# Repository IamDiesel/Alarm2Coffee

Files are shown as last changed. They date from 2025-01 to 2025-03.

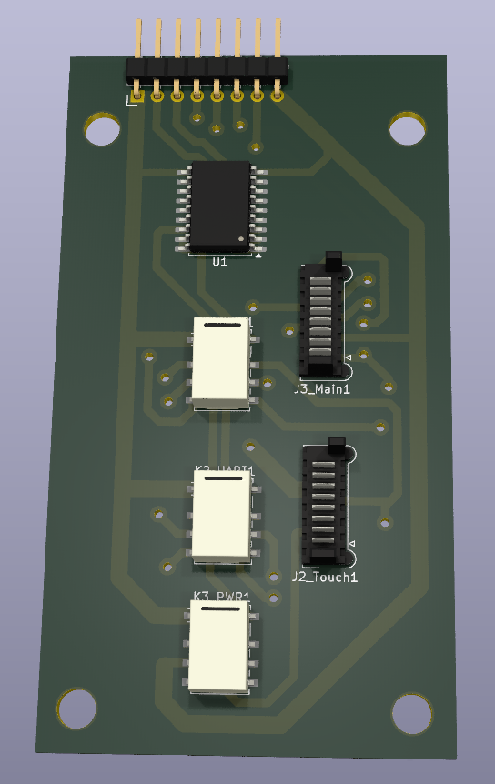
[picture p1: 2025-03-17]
PCB_SCH/PCB_Render.png

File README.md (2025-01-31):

# Power on your Philips 2200 Coffeemachine when your smartphone-alarm goes off - via Raspberry Pi and Home-Assistant #
The following readme describes how to setup a raspberry pi / philips 2200 coffeemachine home assistant automation from scratch (incl. setting up home assistant on a Raspberry Pi5). Btw. thanks to https://github.com/TillFleisch/ESPHome-Philips-Smart-Coffee who gave me some inspiration / information on the coffee machine's UART-protocol.
This project is also capable of displaying the current coffeemachine state and remotly operating the coffeemachine via a smartphone's home assistant app:


### Requirements: ###
- Coffee-Machine: Philips 2200
- MITM (inject & passthrough): Inject coffee selection commands and read current coffee configuration
- Use home assistant for automation and hub to the smartphone alarm
- Additional Fail-Safe mechanism in case RPi is dead and  the MITM configuration must be bridged

### Components used: ###
- Raspberry Pi5 + SD Card
- PicoFlex 90325-0008 socket
- Molex 92315-0815, Picoflex, ribbon cable 150mm
- AZDelivery 3 x 4-Relais Modul 5V
- LUCKFOX DSI Capacitive 7 inch Touch Screen with Case
- Jumper Wire / cables / glue / screws / ...
- If Home Assistant should be connected via wifi: Brostrend AX1800 (External USB Wifi Antenna)

## Install home assistant on Raspberry Pi 5 ##
- Use Pi Imager to flash SD card (see https://developbyter.com/home-assistant-auf-raspberry-pi-installieren-und-einrichten/) 
- create empty file called "ssh" on sd card "bootfs"
- tell router to give RPi a constant IP address
- connect via ssh to RPi (ssh user@ipadress)
- update: sudo apt-get update && sudo apt-get upgrade -y
- install dependencies:
  - sudo apt-get install jq wget curl avahi-daemon udisks2 libglib2.0-bin network-manager dbus apparmor -y
  - sudo apt-get install systemd-journal-remote
- reboot: sudo reboot
- deactivate mac address randomisation:
  - sudo nano /etc/NetworkManager/conf.d/100-disable-wifi-mac-randomization.conf
  - Content:

~~~
[connection]
wifi.mac-address-randomization=1
[device]
wifi.scan-rand-mac-address=no
)
~~~

- install docker & add user:
  
~~~
curl -fsSL https://get.docker.com -o get-docker.sh
sudo sh get-docker.sh
docker –version
sudo usermod -aG docker <user>
~~~

- Download OS-Agent on raspberry pi: wget https://github.com/home-assistant/os-agent/releases/download/1.6.0/os-agent_1.6.0_linux_aarch64.deb
- install: sudo dpkg -i os-agent_1.6.0_linux_aarch64.deb

- install additional dependencies:

~~~
sudo apt install \
apparmor \
bluez \
cifs-utils \
curl \
dbus \
jq \
libglib2.0-bin \
lsb-release \
network-manager \
nfs-common \
systemd-journal-remote \
systemd-resolved \
udisks2 \
wget -y
~~~

- install home assistant superviced (https://github.com/home-assistant/supervised-installer/releases/download/2.0.0/homeassistant-supervised.deb)
  - sudo dpkg -i homeassistant-supervised.deb
  - during installation: choose raspberrypi5-64
  - reboot
- open home assistant in your browser: <ipadress_of_pi>:8123
- download and install smartphone app via QR-Code
- Show home assistant on startup on the 7" display:
  - configure autostart: sudo nano /etc/xdg/lxsession/LXDE-pi/autostart
    - add the following lines:
      
~~~
@unclutter
@xset s off
@xset -dpms
@xset s noblank
@chromium-browser --noerrdialogs --check-for-update-interval=31536000 --disable-infobars --kiosk http://127.0.0.1:8123/
~~~
  if you want to keep a 5min display off timer, use the following settings:
~~~
@unclutter
@xset s off
@xset -dpms
@xset s 300 300
@xset s blank
@chromium-browser --noerrdialogs --check-for-update-interval=31536000 --disable-infobars --kiosk http://127.0.0.1:8123/
~~~

  - activate autologin on pi

~~~
cd /usr/share/hassio/homeassistant/
sudo nano configuration.yaml
~~~

  - add the following lines
    
~~~

homeassistant:
  auth_providers:
    - type: homeassistant
    - type: trusted_networks
      trusted_networks:
        - 192.168.2.0/24  # Example network, adjust to your network range
        - fd00::/8
      trusted_users:
        127.0.0.1: 6a24b8e59e2c45328cd1s97ds0b71221  # Map the IP address to the user ID
        192.168.2.43: 6a24b8249e22445x1cd1797123471221  # Map the IP address to the user ID
      allow_bypass_login: true
  ~~~
  
- install 7inch display (https://wiki.luckfox.com/):
  - sudo nano /boot/config.txt
  - add the following lines:
 
~~~
dtoverlay=vc4-kms-v3d
dtoverlay=vc4-kms-dsi-7inch
~~~
## Install Wifi Antenna ##
Installation guide see https://linux.brostrend.com/
For me, the command from the installation guide threw an error.
Command:
~~~
 sh -c 'wget linux.brostrend.com/install -O /tmp/install && sh /tmp/install'
~~~
Error:
~~~
Setting up initramfs-tools (0.142+rpt3+deb12u1) ...
update-initramfs: deferring update (trigger activated)
Processing triggers for initramfs-tools (0.142+rpt3+deb12u1) ...
update-initramfs: Generating /boot/initrd.img-6.6.62+rpt-rpi-v8
mkinitramfs: failed to determine device for /
mkinitramfs: workaround is MODULES=most, check:
grep -r MODULES /etc/initramfs-tools

Error please report bug on initramfs-tools
Include the output of 'mount' and 'cat /proc/mounts'
update-initramfs: failed for /boot/initrd.img-6.6.62+rpt-rpi-v8 with 1.
dpkg: error processing package initramfs-tools (--configure):
 installed initramfs-tools package post-installation script subprocess returned error exit status 1
Errors were encountered while processing:
 initramfs-tools
E: Sub-process /usr/bin/dpkg returned an error code (1)
Aborting, command failed: apt install --reinstall --yes --no-install-recommends ./rtl8852bu-dkms.deb

===================================================
 ERROR: The driver was NOT successfully installed!
===================================================
1) Please select ALL the text in this terminal, then right click with the
   mouse and select Copy, and finally paste all the text in an email to:
   support@brostrend.com
2) Please also attach this autogenerated log file to the email:
   /tmp/troubleshooting.txt
   If you want to view it, run:
   xdg-open /tmp/troubleshooting.txt
3) Some common issues are documented in:
   https://linux.brostrend.com/troubleshooting/
~~~
Solution:
~~~
sudo nano /etc/initramfs-tools/initramfs.conf
~~~
And set „MODULES=dep“ to „MODULES=most“.
Next, the wifi interface needs to be configured:
- deactivate wlan0: sudo ip link set wlan0 down
- Router: remove static ip for old interface and set static ip for the new interface (e.g. 192.168.2.43)
- In Home Assistant: Go to settings->system->network.
  - Reset configuration for wlan0
  - Set static ip for wlan1
- Configure wifi connection:
  - remove all wlan0 profiles (in GUI top right corner, click on the wifi symbol and delete all wlan0 profiles) 
  - sudo nmtui
  - edit connection
  - select wifi->preconficured --> hit "edit"
  - Find the wlan1 device name (for me it is wlxc83a35b569cd (C8:3A:35:B5:69:CD)
  - Enter SSID
  - Enter WIFI-password
  - set manual ip adress: 192.168.2.43/24
  - set Gateway: your routers ip
  - set DNS servers: your routers ip
 
- If chromium doest start on boot: rm -rf ~/.config/chromium/Singleton*

## configure home assistant ##
### Create entities (German) ###
Create entities (Einstellungen -> Geräte und Dienste -> Helfer)



### Create Automations (German) ###



### setup alarm (Android) ###
- Open the Home Assistant App menu and select Settings
- Go to Companion App
- Select Manage Sensors
- Find the Next Alarm sensor
- Enable the Next Alarm sensor
- Create automation: „Einstellungen“->“Automatisierung & Szenen“->“Automatisierung erstellen““Neue Automatisierung“
  - Auslöser hinzufügen: “Andere Auslöser“-->“Template“
  - Template code:
  
   ~~~
    {{(now()+timedelta(0,60)).strftime('%a %h %d %H:%M %Z %Y') == (((state_attr('sensor.pixel_9_pro_next_alarm', 'Time in Milliseconds') | int / 1000) ) | timestamp_custom('%a %h %d %H:%M %Z %Y'))}}
   ~~~
   
  - add action:


### setup alarm (iOs) ###
The focus sensor can be used to determine when the alarm went off.
- Create iOS shortcut named "HAss focus": deactivate focus
- Create iOS automation that executes the "Hass focus" everytime an alarm goes off
Now the companion app focus sensor of the iOS device can be used to trigger automations in Home-Assistant
- Create Home-Assistant automation:







# Disassemble coffee machine #
The coffee machine's display can be disassembled using a plastic tool.



The wiring between display and mainboard is as follows:



Communication is run via UART @115200
The state of the coffeemachine ist sent from the mainboard to the display. The button events are sent from the display to the mainboard.

# Communication #
## Mainboard -> Display



## Display -> Mainboard



### On / Off ###

~~~
On / Off Beep: d5 55 0a 00 00 03 02 00 00 00 32 25
Power on without cleaning cycle: d5 55 01 00 00 03 02 00 00 00 19 10	
Power Off no Cleaning cycle?: d5550000000302010000210c
~~~

### Drink Selection: ###

~~~
Select Nothing: 		d5 55 00 00 00 03 02 00 00 00 2d 01
Select Espresso:	d5 55 00 00 00 03 02 02 00 00 35 1a 	Nachricht wird 13x gesendet
perl -e 'print pack "H*", "d5550000000302020000351a"' > /dev/ttyUSB2

Hot Water:		d5 55 00 00 00 03 02 04 00 00 1d 36
Select Coffee:		d5 55 00 00 00 03 02 08 00 00 05 2b	Nachricht wird 8x gesendet
Steam:			d5 55 00 00 00 03 02 10 00 00 35 11	Nachricht wird 32x gesendet
~~~

### Settings: ###

~~~

d5 55 00 00 00 03 02 00 02 00 35 18	Bean Size
d5 55 00 00 00 03 02 00 04 00 1c 32	Coffee Size
Play:
d5 55 00 00 00 03 02 00 00 01 25 05 	Play-Button (espresso, 39x)
perl -e 'print pack "H*", "d55500000003020000012505"' > /dev/ttyUSB2
~~~

For both mainboard messages and display messages the CRC algorithm is currently unknown. So it might be necessary to record the messages individually.

## Connect relais, UART and power ##

The relayboard 1 is used as a failsafe when the pi does not power on. In that case the UART connection will be without the MITM and therby the mainboard is directly connected to the display. When the relay is activated the raspberry pi acts as MITM between mainboard and display.
Relayboard 2 is used to reset the display when activated via power on command incection. A power cycle will activate the display. This relay is also failsafe for the case, that RPi is powered off, since Display GND is connected to the Relay-Normally-Closed Pin and Relay-Common is connected to the Mainboard GND.
Here is the connection diagram:



## Activate UART2/3 and GPIO on RPi5 & ## 

Add the following lines via "sudo nano /boot/config.txt":



As a result the GPIO configuration will be as follows:
- ttyAMA2	Display	Pin 7 (GPIO 4)	TX
- ttyAMA2	Display	Pin 29 (GPIO 5)	RX
- ttyAMA3	Mainboard	Pin 24 (GPIO 8)	TX
- ttyAMA3	Mainboard	Pin 21 (GPIO 9)	RX

- In order to use GPIO on RPi5 another package is required: .coffee/bin/pip install rpi-lgpio
- It could be necessary to uninstall the RPi GPIO first: .coffee/bin/pip uninstall Rpi.GPIO

## Setup Home Assistant API / install the required python packages ##

- Create a longliving HAss token in HAss: Profil->Sicherheit
  - safe this token in a file called "HASS_Token.py" with: token = "asdjalksdjkasjdklasjd your token asdlkalösdkaölsd"
- Create venv:  python3 -m venv .coffee
- install Home assistant: .coffee/bin/pip install homeassistant_api
- install pyserial: .coffee/bin/pip install pyserial

## Home Assistant WIFI Stability Issues ##
Home Assistant started beeing offline from time to time. Where the device was not reachable via ssh or the home assistant app.
The only thing that seemed to help was a wifi reset. So I wrote a little script that (e.g.) pings the local router. In case the router is not reachable the script will reset wifi, making the HAss available again.

## Finish ##

WhatsApp Bild 2025-01-12 um 21 23 38_4eb5911e

- Thats it. Now run Philips_2200.py and the RPI will inject the respective display commands, when the respective Home Assistant buttons are pushed. If no button is pushed, the RPi will forward all messages from display to mainboard and vice versa. In Addition a alarm will trigger a power on command sent to the coffee machine.
- the relay boards fit nicely behind the display. I glued screws on the backside of the display module in order to fit the relay boards to the display.
- In order to run the python script on startup the following lines can be added to rc.local via sudo nano /etc/rc.local:
~~~
sudo bash -c '/home/youruser/.coffee/bin/python3 /home/youruser/Documents/philips_pi/Philips_2200.py > /home/fuchsi/Documents/philips_pi/alarm2coffee.log 2>&1' &
~~~
Of course the path must be set to your local Philips_2200.py. In addition Wifi_Reset.py must be in the same folder as Philips_2200.py.
- Also a dashboard can be created in order to interact with the coffeemachine via smartphone. Here is mine:

~~~

views:
  - type: sections
    max_columns: 2
    title: Kaffee
    path: kaffee
    icon: mdi:coffee
    sections:
      - type: grid
        cards:
          - type: tile
            entity: input_button.philips_display_power_btn
            name: Power On
            icon_tap_action:
              action: toggle
            tap_action:
              action: toggle
            hide_state: true
          - type: tile
            entity: input_button.philips_display_power_off_btn
            name: Power Off
            tap_action:
              action: toggle
            hide_state: true
          - show_name: true
            show_icon: true
            type: button
            tap_action:
              action: perform-action
              perform_action: automation.trigger
              target:
                entity_id: automation.philips_display_steam_event_helper
              data:
                skip_condition: true
            entity: input_boolean.philips_mainboard_espresso_led
            show_state: false
            name: Espresso
            icon: mdi:cup
          - show_name: true
            show_icon: true
            type: button
            tap_action:
              action: perform-action
              perform_action: automation.trigger
              target:
                entity_id: automation.philips_event_coffee_btn
              data:
                skip_condition: true
            entity: input_boolean.philips_mainboard_coffee_led
            show_state: false
            name: Coffee
            icon: mdi:coffee
          - show_name: true
            show_icon: true
            type: button
            tap_action:
              action: perform-action
              perform_action: automation.trigger
              target:
                entity_id: automation.philips_event_hot_water_btn
              data:
                skip_condition: true
            entity: input_boolean.philips_mainboard_hot_water_led
            show_state: false
            name: Hot Water
            icon: mdi:tea-outline
          - show_name: true
            show_icon: true
            type: button
            tap_action:
              action: perform-action
              perform_action: automation.trigger
              target:
                entity_id: automation.neue_automatisierung
              data:
                skip_condition: true
            entity: input_boolean.philips_mainboard_steam_led
            show_state: false
            name: Steam
            icon: mdi:weather-windy
      - type: grid
        cards:
          - show_name: true
            show_icon: true
            type: button
            tap_action:
              action: toggle
            entity: input_button.input_button_philips_display_play_btn
            grid_options:
              columns: 12
              rows: 2
            name: Start
          - type: conditional
            conditions:
              - condition: state
                entity: input_select.philips_bean_led
                state: '1'
            grid_options:
              columns: 6
              rows: 1
            card:
              show_name: true
              show_icon: true
              type: button
              tap_action:
                action: toggle
              entity: input_button.philips_display_bean_btn
              icon: mdi:network-strength-1
              hold_action:
                action: toggle
              name: Strength
          - type: conditional
            conditions:
              - condition: state
                entity: input_select.philips_bean_led
                state: '2'
            grid_options:
              columns: 6
              rows: 1
            card:
              show_name: true
              show_icon: true
              type: button
              tap_action:
                action: toggle
              entity: input_button.philips_display_bean_btn
              icon: mdi:network-strength-3
              hold_action:
                action: toggle
              name: Strength
          - type: conditional
            conditions:
              - condition: state
                entity: input_select.philips_bean_led
                state: '3'
            grid_options:
              columns: 6
              rows: 1
            card:
              show_name: true
              show_icon: true
              type: button
              tap_action:
                action: toggle
              entity: input_button.philips_display_bean_btn
              icon: mdi:network-strength-4
              hold_action:
                action: toggle
              name: Strength
          - type: conditional
            conditions:
              - condition: state
                entity: input_select.philips_bean_led
                state: 'Off'
            grid_options:
              columns: 6
              rows: 1
            card:
              show_name: true
              show_icon: true
              type: button
              tap_action:
                action: none
              entity: input_button.philips_display_bean_btn
              icon: mdi:cancel
              hold_action:
                action: none
              name: Strength
          - type: conditional
            conditions:
              - condition: state
                entity: input_select.philips_cup_size_led
                state: '1'
            grid_options:
              columns: 6
              rows: 1
            card:
              show_name: true
              show_icon: true
              type: button
              tap_action:
                action: toggle
              entity: input_button.philips_display_cup_btn
              icon: mdi:network-strength-1
              hold_action:
                action: toggle
              name: Size
          - type: conditional
            conditions:
              - condition: state
                entity: input_select.philips_cup_size_led
                state: '2'
            grid_options:
              columns: 6
              rows: 1
            card:
              show_name: true
              show_icon: true
              type: button
              tap_action:
                action: toggle
              entity: input_button.philips_display_cup_btn
              icon: mdi:network-strength-3
              hold_action:
                action: toggle
              name: Size
          - type: conditional
            conditions:
              - condition: state
                entity: input_select.philips_cup_size_led
                state: '3'
            grid_options:
              columns: 6
              rows: 1
            card:
              show_name: true
              show_icon: true
              type: button
              tap_action:
                action: toggle
              entity: input_button.philips_display_cup_btn
              icon: mdi:network-strength-4
              hold_action:
                action: toggle
              name: Size
          - type: conditional
            conditions:
              - condition: state
                entity: input_select.philips_cup_size_led
                state: 'Off'
            grid_options:
              columns: 6
              rows: 1
            card:
              show_name: true
              show_icon: true
              type: button
              tap_action:
                action: none
              entity: input_button.philips_display_cup_btn
              icon: mdi:cancel
              hold_action:
                action: none
              name: Size
          - type: conditional
            conditions:
              - condition: state
                entity: input_boolean.philips_double_coffee_led
                state: 'on'
            grid_options:
              columns: 6
              rows: 1
            card:
              show_name: true
              show_icon: true
              type: button
              tap_action:
                action: none
              entity: input_boolean.philips_double_coffee_led
              name: Coffee
              hold_action:
                action: none
              icon: mdi:dice-2
          - type: conditional
            conditions:
              - condition: state
                entity: input_boolean.philips_double_espresso_led
                state: 'on'
            grid_options:
              columns: 6
              rows: 1
            card:
              show_name: true
              show_icon: true
              type: button
              tap_action:
                action: none
              entity: input_boolean.philips_double_coffee_led
              name: Espresso
              hold_action:
                action: none
              icon: mdi:dice-2
          - type: conditional
            conditions:
              - condition: state
                entity: input_select.philipps_water_empty_led
                state: Water empty
            grid_options:
              columns: 6
              rows: 1
            card:
              show_name: true
              show_icon: true
              type: button
              tap_action:
                action: none
              entity: input_select.philipps_water_empty_led
              name: No Water
              hold_action:
                action: none
              icon: mdi:water-off
          - type: conditional
            conditions:
              - condition: state
                entity: input_select.philipps_error_led
                state: Waste full
            grid_options:
              columns: 6
              rows: 1
            card:
              show_name: true
              show_icon: true
              type: button
              tap_action:
                action: none
              entity: input_boolean.philips_waste_helper_led
              name: Waste full
              hold_action:
                action: none
              icon: mdi:delete-variant
          - type: conditional
            conditions:
              - condition: state
                entity: input_select.philipps_error_led
                state: Error active
            grid_options:
              columns: 6
              rows: 1
            card:
              show_name: true
              show_icon: true
              type: button
              tap_action:
                action: none
              entity: input_boolean.philips_error_helper_led
              name: Error
              hold_action:
                action: none
              icon: mdi:alert-circle
        column_span: 1
      - type: grid
        cards:
          - type: heading
            heading_style: title
            icon: mdi:alarm
            badges:
              - type: entity
                entity: input_boolean.philips_alarm_daniel
              - type: entity
                entity: sensor.pixel_9_pro_next_alarm
              - type: entity
                show_state: true
                show_icon: true
                entity: input_boolean.philips_alarm_fox
            heading: Mit Wecker einschalten
          - type: tile
            entity: input_boolean.philips_alarm_daniel
            tap_action:
              action: toggle
            name: Alarm2Coffee Daniel
            grid_options:
              columns: 12
              rows: 1
          - type: tile
            entity: input_boolean.philips_alarm_fox
            tap_action:
              action: toggle
            name: Alarm2Coffee Fox
            grid_options:
              columns: 12
              rows: 1
          - type: tile
            entity: sensor.pixel_9_pro_next_alarm
            grid_options:
              columns: 12
              rows: 2
            name: Nächster Wecker Daniel
            hide_state: false
            show_entity_picture: false
            vertical: true
            state_content:
              - state
              - Local Time

~~~

# TODOs #
- [ ] Create relay-circuit-board to avoid messy wiring (also 3 relays are unused)
- [ ] Refactor python software
  - [x] check for HAss availability on startup
  - [ ] refactor SW components (file / component is too big)
  - [ ] further evaluate power cycle code
  - [x] Read coffee strength and display this information in home assistant
  - [x] Read cup size and display this information in home assistant
  - [x] Read 1x / 2x and drink selection information and display this information in home assistant
  - [x] Check Home Assistant loosing WIFI connection to home net
    - [x] Write script to reset wifi when loosing connection to gateway
    - [x] evaluate power settings

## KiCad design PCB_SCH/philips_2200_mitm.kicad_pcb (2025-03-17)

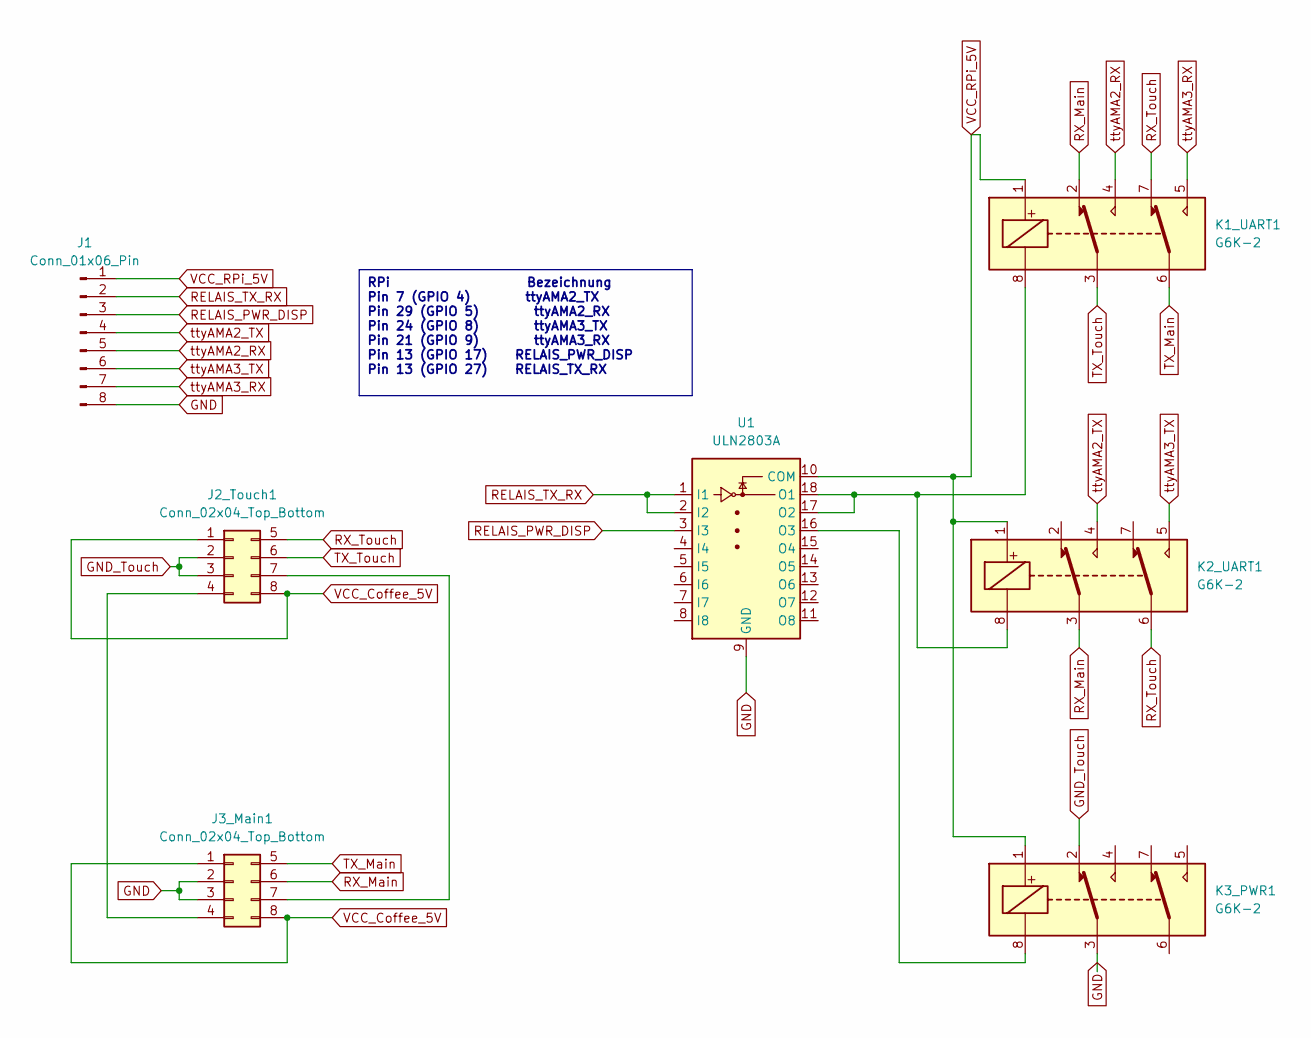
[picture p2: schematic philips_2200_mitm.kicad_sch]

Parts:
J1: Conn_01x06_Pin; PinHeader_1x08_P2.54mm_Horizontal
J2_Touch1, J3_Main1: Conn_02x04_Top_Bottom; Molex_Picoflex_90325-0008_2x04_P1.27mm_Vertical
K1_UART1, K2_UART1, K3_PWR1: G6K-2; Relay_DPDT_Omron_G6K-2F-Y
U1: ULN2803A; SOIC-18W_7.5x11.6mm_P1.27mm

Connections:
GND: J1.8, J3_Main1.2, J3_Main1.3, K3_PWR1.3, U1.9 (GND)
GND_Touch: J2_Touch1.2, J2_Touch1.3, K3_PWR1.2
unnamed: J2_Touch1.4, J3_Main1.4
unnamed: J2_Touch1.7, J3_Main1.7
unnamed: K1_UART1.8, K2_UART1.8, U1.17 (O2), U1.18 (O1)
unnamed: K3_PWR1.8, U1.16 (O3)
RELAIS_PWR_DISP: J1.3, U1.3 (I3)
RELAIS_TX_RX: J1.2, U1.1 (I1), U1.2 (I2)
RX_Main: J3_Main1.6, K1_UART1.2, K2_UART1.3
RX_Touch: J2_Touch1.5, K1_UART1.7, K2_UART1.6
TX_Main: J3_Main1.5, K1_UART1.6
TX_Touch: J2_Touch1.6, K1_UART1.3
VCC_Coffee_5V: J2_Touch1.1, J2_Touch1.8, J3_Main1.1, J3_Main1.8
VCC_RPi_5V: J1.1, K1_UART1.1, K2_UART1.1, K3_PWR1.1, U1.10 (COM)
ttyAMA2_RX: J1.5, K1_UART1.4
ttyAMA2_TX: J1.4, K2_UART1.4
ttyAMA3_RX: J1.7, K1_UART1.5
ttyAMA3_TX: J1.6, K2_UART1.5

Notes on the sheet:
RPi Bezeichnung Pin 7 (GPIO 4) ttyAMA2_TX Pin 29 (GPIO 5) ttyAMA2_RX Pin 24 (GPIO 8) ttyAMA3_TX Pin 21 (GPIO 9) ttyAMA3_RX Pin 13 (GPIO 17) RELAIS_PWR_DISP Pin 13 (GPIO 27) RELAIS_TX_RX

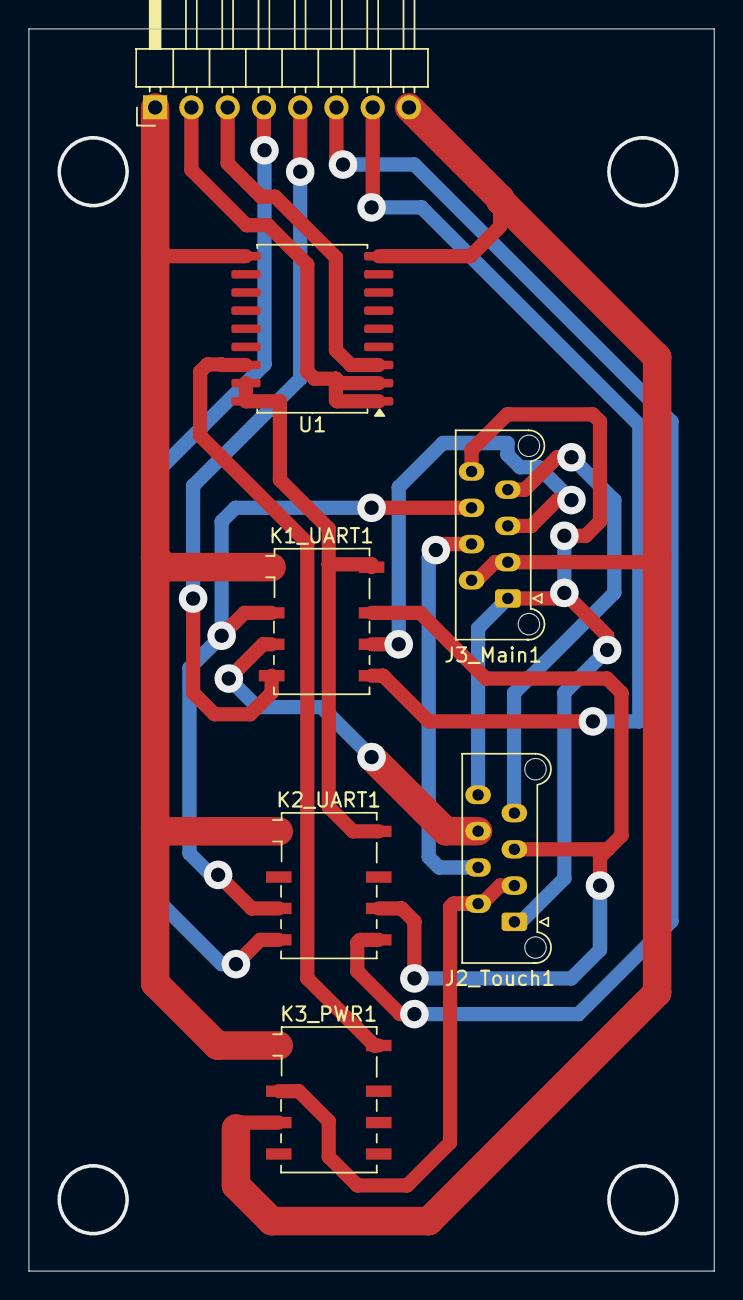
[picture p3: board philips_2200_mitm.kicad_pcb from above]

Board: 2 copper layers, 48.0 x 87.0 mm, 7 parts (0 on the bottom side), 18 nets.

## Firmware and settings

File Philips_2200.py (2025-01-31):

import os
from homeassistant_api import Client, State, errors
import serial
import subprocess
import sys
from HASS_Token import token
import RPi.GPIO as GPIO
import time
from threading import Thread
from Reset_Wifi import Wifi_Deamon

printSerial = False

class Philips_2200(Thread):
    def __init__(self,persistant_HASS_token, sn_serial_main=None, sn_serial_disp=None):

        GPIO.setmode(GPIO.BCM)  # GPIO Nummern statt Board Nummern
        self.RELAIS_PWR_DISP_GPIO = 17
        self.RELAIS_TX_RX_GPIO = 27 #RELAIS ON = MITM mode, #RELAIS Off = Normal mode

        self.sn_serial_main = sn_serial_main
        self.sn_serial_disp = sn_serial_disp
        
        self.persistant_HASS_token = persistant_HASS_token
        
        #send repetitions for the display commands
        self.cmd_rep = 20

        #mainboard protocol state definitions (mainboard -> display)
        self.preAmbelStates = {0xd5:'correct_0',0x55:'correct_1'}
        self.statesDrinkSelection = {0x00: 'Off', 0x03: 'Half Brightness', 0x07: 'Full Brightness', 0x38: 'Double', 0x3F:'Full Brightness'}
        self.beanLEDStates = {0x00:'1LED/Off', 0x38:'2LED', 0x3F:'3LED'}
        self.beanLEDStatesCtrl = {0x07: 'Show LED Group', 0x38: 'Powder Selected', 0x00:'Off'}
        self.sizeLEDStates = {0x00:'1LED/Off', 0x38:'2LED', 0x3F:'3LED', 0x07: 'TopLED'}
        self.sizeAquaLEDStates = {0x00: 'Off', 0x07:'Show LED Group',0x38:'Aqua Clean Orange'}
        self.calcCleanLEDStates = {0x00: 'Both Off', 0x38:'Calc / Clean orange', 0x07:'unknown'}
        self.emptyWaterLEDStates = {0x00: 'No error', 0x38:'Water empty'}
        self.wasteWarningLEDStates = {0x00: 'No error', 0x07:'Waste full', 0x38:'Error active'}
        self.playPauseLEDStates = {0x00:'Off', 0x07:'On'}
        
        #mainboard protocol (mainboard -> display)
        self.protocol = {0:self.preAmbelStates, 1:self.preAmbelStates,3:self.statesDrinkSelection, 4:self.statesDrinkSelection, 5:self.statesDrinkSelection, 6:self.statesDrinkSelection, 8:self.beanLEDStates, 9:self.beanLEDStatesCtrl, 10:self.sizeLEDStates, 11:self.sizeAquaLEDStates, 12:self.calcCleanLEDStates, 14:self.emptyWaterLEDStates, 15:self.wasteWarningLEDStates, 16:self.playPauseLEDStates}
        self.protocolNames = {0:'Pre_0',1:'Pre_1', 3:'Espresso LED', 4:'Hot Water LED', 5:'Coffe LED', 6:'Steam LED', 8:'Bean LED 0', 9:'Bean LED 1', 10:'Size LED', 11:'Size Aqua LED', 12:'Calc Clean', 14:'Water LED', 15:'Waste / Warning', 16:'Play LED'}
    
        #init serial
        if(sn_serial_main is None or sn_serial_disp is None):
            self.ser_display="/dev/ttyAMA2"
            self.ser_mainboard="/dev/ttyAMA3"
        else:           
            self.sn_serial_main = sn_serial_main
            self.sn_serial_disp = sn_serial_disp
            self.ser_mainboard = self.getSerialDeviceBySerialnumber(self.sn_mainboard)#"/dev/ttyUSB0" #TX_mainboard to RX_Pi_0, RX_mainboard to TX_Pi_0 
            self.ser_display = self.getSerialDeviceBySerialnumber(self.sn_display)
        self.__init_serial()
        self.__init_relais()
        self.__relais_on()
        
        self._running = False
        
        #helper for reading and setting HASS entities, blocks program until HAss is online
        self.hass_helper = self.HASS_Helper(self.persistant_HASS_token)
        #if a button was pressed inside HASS, this variable will be set to the corresponding display serial command
        self.next_cmd = None
        super(Philips_2200, self).__init__()

        #TODO enable relais for intercepting TX/RX

    def __init_serial(self):

        try:
            self.dev_display = serial.Serial(self.ser_display, write_timeout=1)   
            self.dev_mainboard = serial.Serial(self.ser_mainboard,write_timeout=1)
            self.dev_mainboard.baudrate = 115200
            self.dev_mainboard.bytesize = 8
            self.dev_mainboard.parity = 'N'
            self.dev_mainboard.stopbits = 1
            self.dev_display.baudrate = 115200
            self.dev_display.bytesize = 8
            self.dev_display.parity = 'N'
            self.dev_display.stopbits = 1
        except serial.SerialException:
            self.dev_display.close()
            self.dev_mainboard.close()
            self.__relais_off(self)
    
    def __init_relais(self):
        GPIO.setmode(GPIO.BCM)  # GPIO Nummern statt Board Nummern
        GPIO.setup(self.RELAIS_PWR_DISP_GPIO, GPIO.OUT)  # GPIO Modus zuweisen
        GPIO.setup(self.RELAIS_TX_RX_GPIO, GPIO.OUT)  # GPIO Modus zuweisen
    
    def __relais_on(self):
        GPIO.output(self.RELAIS_PWR_DISP_GPIO, GPIO.HIGH)  # LOW-Pegel --> Relais An	 (Normally Off connected)
        GPIO.output(self.RELAIS_TX_RX_GPIO, GPIO.LOW)
    
    def __relais_off(self):
        GPIO.output(self.RELAIS_PWR_DISP_GPIO, GPIO.HIGH)  # LOW-Pegel --> Relais An	 (Normally Off connected)
        GPIO.output(self.RELAIS_TX_RX_GPIO, GPIO.HIGH)
    
    def __relais_pwr_toggle(self, t_off):
        GPIO.output(self.RELAIS_PWR_DISP_GPIO, GPIO.LOW)  # PWR Display Off, GND not connected
        time.sleep(t_off)
        GPIO.output(self.RELAIS_PWR_DISP_GPIO, GPIO.HIGH)  # PWR Display On, GND connected
        #time.sleep(t_off)

    # display commands (display->mainboard:

    def forward_mainboard_to_display_update_hass(self):
        if (self.dev_mainboard.inWaiting() >= 19):
            input_main = self.dev_mainboard.read(19)
            self.dev_mainboard.write(input_main)
            self.update_HASS_LED(input_main)
            return 1
        return 0

    def select_coffee_cmd_routine(self):
        cmd_select_coffee = b'\xd5\x55\x00\x00\x00\x03\x02\x08\x00\x00\x05\x2b'
        for i in range(self.cmd_rep):
            self.dev_display.write(cmd_select_coffee)
            self.forward_mainboard_to_display_update_hass()
    def select_espresso_cmd_routine(self):
        cmd_select_espresso = b'\xd5\x55\x00\x00\x00\x03\x02\x02\x00\x00\x35\x1a'
        for i in range(self.cmd_rep):
            self.dev_display.write(cmd_select_espresso)
            self.forward_mainboard_to_display_update_hass()
    def select_hot_water_cmd_routine(self):
        cmd_select_hot_water = b'\xd5\x55\x00\x00\x00\x03\x02\x04\x00\x00\x1d\x36'
        for i in range(self.cmd_rep):
            self.dev_display.write(cmd_select_hot_water)
            self.forward_mainboard_to_display_update_hass()
    def select_steam_cmd_routine(self):
        cmd_select_steam = b'\xd5\x55\x00\x00\x00\x03\x02\x10\x00\x00\x35\x11'
        for i in range(self.cmd_rep):
            self.dev_display.write(cmd_select_steam)
            self.forward_mainboard_to_display_update_hass()
    def select_play_cmd_routine(self):
        cmd_select_play = b'\xd5\x55\x00\x00\x00\x03\x02\x00\x00\x01\x25\x05'
        for i in range(self.cmd_rep):
            self.dev_display.write(cmd_select_play)
            self.forward_mainboard_to_display_update_hass()

    def power_off_no_clean_cmd_routine(self):
        cmd_power_off = b'\xd5\x55\x00\x00\x00\x03\x02\x01\x00\x00\x21\x0c'
        for i in range(self.cmd_rep):
            self.dev_display.write(cmd_power_off)
            self.forward_mainboard_to_display_update_hass()

    def select_bean_cmd_routine(self):
        cmd_select_bean_size = b'\xd5\x55\x00\x00\x00\x03\x02\x00\x02\x00\x35\x18'
        for i in range(self.cmd_rep):
            self.dev_display.write(cmd_select_bean_size)
            self.forward_mainboard_to_display_update_hass()
    def select_cup_cmd_routine(self):
        cmd_select_cup_size = 	b'\xd5\x55\x00\x00\x00\x03\x02\x00\x04\x00\x1c\x32'
        for i in range(self.cmd_rep):
            self.dev_display.write(cmd_select_cup_size)
            self.forward_mainboard_to_display_update_hass()
    def power_on_cmd_routine(self, clean=True):
        cmd_beep = b'\xd5\x55\x0a\x00\x00\x03\x02\x00\x00\x00\x32\x25'
        if(clean):
            cmd_power_on = b'\xd5\x55\x02\x01\x02\x00\x02\x00\x00\x00\x38\x15'
        else:
            cmd_power_on = b'\xd5\x55\x01\x00\x00\x03\x02\x00\x00\x00\x19\x10'
        cmd_select_nothing = 	b'\xd5\x55\x00\x00\x00\x03\x02\x00\x00\x00\x2d\x01'
        self.__relais_pwr_toggle(0.4)#0.485
        for i in range(23): #23 from recording
            self.dev_display.write(cmd_beep)
        #TODO test
        #send power on command from DisplayIntercept to Maiboard until the mainboard sends messages to the display
        count = 0
        while(self.dev_mainboard.inWaiting() <= 0):
            if(count < 7500):#150
                self.dev_display.write(cmd_power_on)
            count +=1
            if(count > 10000):
                print("No response from Mainboard to power on message")
                break
        print(count)
        #time.sleep(1)
        count_iter = 0
        count_disp_msg = 0
        count_main_msg = 0
        #time.sleep(1)
        count_toggle = 0
        while(True):
            count_iter +=1   
            time.sleep(0.5)
            
            while(self.dev_display.inWaiting() > 0):
                if (self.dev_display.read(1) == b'\xd5'): #Startbit received                                         
                    if (self.dev_display.inWaiting() >= 11): #In case there is data and startbit was received: Forward Display->Mainboard
                        count_disp_msg +=1
                        input_disp = b'\xd5' + self.dev_display.read(11)
                        #print("D: "+ " ".join(format(x, "02x") for x in input_disp))
                        count_main_msg += self.forward_mainboard_to_display_update_hass()
                        self.dev_display.write(input_disp)
                        
                        if(count_disp_msg >= 200):
                            break
                        
            if(count_disp_msg + count_main_msg >= 200):
                break
            if(count_iter%3==0):
                self.__relais_pwr_toggle(0.4)#0.485
                count_disp_msg = 0
                count_main_msg = 0
                count_toggle +=1
                print("DISP-PWR toggle")
                if(count_toggle>10):
                    print("Activating Display by PWR-toggle failed")
                    break
            count_disp_msg = 0
            count_main_msg = 0
            print("Waiting for disp")


    '''TODO implement cmd routines
    -DONE power_off_no_clean_cmd_routine
    -power_off_clean_cmd_routine
    -power_on_clean_cmd_routine
    -DONE select_bean_cmd_routine
    -DONE select_cup_cmd_routine
    '''

    class HASS_Helper:
        #helper for i/o from and to homeassistant
        def __init__(self, persistant_HASS_token):
            self.persistant_HASS_token = persistant_HASS_token
            self.URL = "http://localhost:8123/api"
            self.wait_for_api()
            
        def wait_for_api(self):
            exception_thrown = True
            while(exception_thrown):
                try:
                    self.get_entity_state("binary_sensor.rpi_power_status")
                    exception_thrown = False
                    time.sleep(15)
                except errors.EndpointNotFoundError:
                    time.sleep(15)
                    print("Waiting for API")
                    continue
                except Exception:
                    time.sleep(15)
                    print("Waiting for API")
                    continue
        
        def set_entity_state(self,entity_id, value):
            client = Client(self.URL, self.persistant_HASS_token)
            client.set_state(State(state=value, entity_id=entity_id))
            
        def get_entity_state(self, entity_id):
            client = Client(self.URL, self.persistant_HASS_token) 
            entity = client.get_entity(entity_id=entity_id) #session is closed after this call
            return entity.get_state().state

    def getSerialDeviceBySerialnumber(self, serialnumber):
        device = None
        for i in range(10):
            tmpDevice = f'/dev/ttyUSB{i}'
            command = f'/bin/udevadm info --name={tmpDevice} | grep ID_USB_SERIAL_SHORT'
            try:
                result = subprocess.check_output(command, shell = True, executable = "/bin/bash", stderr = subprocess.STDOUT)
                #print(result.splitlines()[0].decode())
                if(result.splitlines()[0].decode().split('=')[1] == serialnumber):
                    #print(f"Found Device with S/N [{serialnumber}]: {tmpDevice}")
                    device = tmpDevice
            except subprocess.CalledProcessError as cpe:
                result = cpe.output
                #print(result)
                continue
        return device

    def update_HASS_LED(self,input):
        try:
            #espresso LED
            rd_led_state ='on'
            if(self.protocol[3][int(hex(input[3]),0)] == 'Off'):
                rd_led_state = 'off'
            elif(self.protocol[3][int(hex(input[3]),0)] == 'Double'):
                self.hass_helper.set_entity_state('input_boolean.philips_double_espresso_led','on')
            else:
                self.hass_helper.set_entity_state('input_boolean.philips_double_espresso_led','off')
            self.hass_helper.set_entity_state('input_boolean.philips_mainboard_espresso_led',rd_led_state)
            
            #hot water
            rd_led_state ='on'
            if(self.protocol[4][int(hex(input[4]),0)] == 'Off'):
                rd_led_state = 'off'
            self.hass_helper.set_entity_state('input_boolean.philips_mainboard_hot_water_led',rd_led_state)

            #coffee
            rd_led_state ='on'
            if(self.protocol[5][int(hex(input[5]),0)] == 'Off'):
                rd_led_state = 'off'
            elif(self.protocol[5][int(hex(input[5]),0)] == 'Double'):
                self.hass_helper.set_entity_state('input_boolean.philips_double_coffee_led','on')
            else:
                self.hass_helper.set_entity_state('input_boolean.philips_double_coffee_led','off')
            self.hass_helper.set_entity_state('input_boolean.philips_mainboard_coffee_led',rd_led_state)
            
            #steam
            rd_led_state ='on'
            if(self.protocol[6][int(hex(input[6]),0)] == 'Off'):
                rd_led_state = 'off'
            self.hass_helper.set_entity_state('input_boolean.philips_mainboard_steam_led',rd_led_state)
 
            #Water empty
            rd_led_state ='No error'
            if(self.protocol[14][int(hex(input[14]),0)] == 'Water empty'):
                  rd_led_state = 'Water empty'
            self.hass_helper.set_entity_state('input_select.philipps_water_empty_led',rd_led_state)
            
            #Error LED
            #self.wasteWarningLEDStates = {0x00: 'No error', 0x07:'Waste full', 0x38:'Error active'}
            self.hass_helper.set_entity_state('input_select.philipps_error_led',self.protocol[15][int(hex(input[15]),0)])
            
            #Cup Size
            #self.sizeLEDStates = {0x00:'1LED/Off', 0x38:'2LED', 0x3F:'3LED', 0x07: 'TopLED'}
            #elf.sizeAquaLEDStates = {0x00: 'Off', 0x07:'Show LED Group',0x38:'Aqua Clean Orange'}
            if(self.protocol[11][int(hex(input[11]),0)] == 'Off'):
                if(self.protocol[10][int(hex(input[10]),0)] == '1LED/Off'):
                    self.hass_helper.set_entity_state('input_select.philips_cup_size_led','Off')
            elif(self.protocol[11][int(hex(input[11]),0)] == 'Show LED Group'):
                match self.protocol[10][int(hex(input[10]),0)]:
                    case '1LED/Off': rd_led_state = '1'
                    case '2LED': rd_led_state = '2'
                    case '3LED': rd_led_state = '3'
                    case 'TopLED': rd_led_state = 'TopLED'
                    case _: rd_led_state = 'Off'
                self.hass_helper.set_entity_state('input_select.philips_cup_size_led',rd_led_state)       
            #Off: sizeLED = 1LED/Off + sizeAqua = Off 
            #1LED: sizeLED = 1LED/Off + sizeAqua != Off
            #2LED: sizeLED = 2LED + sizeAqua != Off
            #3LED: sizeLED = 3LED + sizeAqua != Off
            
            #bean strength
            #        self.beanLEDStates = {0x00:'1LED/Off', 0x38:'2LED', 0x3F:'3LED'}
            #       self.beanLEDStatesCtrl = {0x07: 'Show LED Group', 0x38: 'Powder Selected', 0x00:'Off'}
            if(self.protocol[9][int(hex(input[9]),0)] == 'Off'):
                if(self.protocol[8][int(hex(input[8]),0)] == '1LED/Off'):
                    self.hass_helper.set_entity_state('input_select.philips_bean_led','Off')
            elif(self.protocol[9][int(hex(input[9]),0)] == 'Show LED Group'):
                match self.protocol[8][int(hex(input[8]),0)]:
                    case '1LED/Off': rd_led_state = '1'
                    case '2LED': rd_led_state = '2'
                    case '3LED': rd_led_state = '3'
                    case _: rd_led_state = 'Off'
                self.hass_helper.set_entity_state('input_select.philips_bean_led',rd_led_state)  
            elif(self.protocol[9][int(hex(input[9]),0)] == 'Powder Selected'):
                self.hass_helper.set_entity_state('input_select.philips_bean_led','Powder')
                
            
            
            """
                   self.statesDrinkSelection = {0x00: 'Off', 0x03: 'Half Brightness', 0x07: 'Full Brightness', 0x38: 'Double', 0x3F:'Full Brightness'}
        self.beanLEDStates = {0x00:'1LED/Off', 0x38:'2LED', 0x3F:'3LED'}
        self.beanLEDStatesCtrl = {0x07: 'Show LED Group', 0x38: 'Powder Selected', 0x00:'Off'}
        self.sizeLEDStates = {0x00:'1LED/Off', 0x38:'2LED', 0x3F:'3LED', 0x07: 'TopLED'}
        self.sizeAquaLEDStates = {0x00: 'Off', 0x07:'Show LED Group',0x38:'Aqua Clean Orange'}
        self.calcCleanLEDStates = {0x00: 'Both Off', 0x38:'Calc / Clean orange', 0x07:'unknown'}
        self.emptyWaterLEDStates = {0x00: 'No error', 0x38:'Water empty'}
        self.wasteWarningLEDStates = {0x00: 'No error', 0x07:'Waste full', 0x38:'Error active'}
        self.playPauseLEDStates = {0x00:'Off', 0x07:'On'}
        
        #mainboard protocol (mainboard -> display)
        self.protocol = {0:self.preAmbelStates, 1:self.preAmbelStates,3:self.statesDrinkSelection, 4:self.statesDrinkSelection, 5:self.statesDrinkSelection, 6:self.statesDrinkSelection, 8:self.beanLEDStates, 9:self.beanLEDStatesCtrl, 10:self.sizeLEDStates, 11:self.sizeAquaLEDStates, 12:self.calcCleanLEDStates, 14:self.emptyWaterLEDStates, 15:self.wasteWarningLEDStates, 16:self.playPauseLEDStates}
        self.protocolNames = {0:'Pre_0',1:'Pre_1', 3:'Espresso LED', 4:'Hot Water LED', 5:'Coffe LED', 6:'Steam LED', 8:'Bean LED 0', 9:'Bean LED 1', 10:'Size LED', 11:'Size Aqua LED', 12:'Calc Clean', 14:'Water LED', 15:'Waste / Warning', 16:'Play LED'}
            """
        except KeyError:
            print("key error")
        except Exception:
            self.__relais_off()
            
    def read_HASS_button_actions(self):
        self.next_cmd = None
        try:
            power_action = self.hass_helper.get_entity_state('input_boolean.philips_display_power_btn_event')
            power_action_nc = self.hass_helper.get_entity_state('input_boolean.philips_display_power_nc_btn_event')
            espresso_action = self.hass_helper.get_entity_state('input_boolean.philips_display_espresso_btn')
            coffee_action = self.hass_helper.get_entity_state('input_boolean.philips_display_coffee_btn_event')
            water_action = self.hass_helper.get_entity_state('input_boolean.philips_display_hot_water_btn_event')
            steam_action = self.hass_helper.get_entity_state('input_boolean.philips_display_steam_btn_event')
            play_action = self.hass_helper.get_entity_state('input_boolean.philips_display_play_btn_event')
            cup_action = self.hass_helper.get_entity_state('input_boolean.philips_display_cup_btn_event')
            bean_action = self.hass_helper.get_entity_state('input_boolean.philips_display_bean_btn_event')
            off_action = self.hass_helper.get_entity_state('input_boolean.philips_display_power_off_btn_event')
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

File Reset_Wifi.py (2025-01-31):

import os
import time
from threading import Thread

class Wifi_Deamon(Thread):
    def __init__(self, gateway_ip):
        self._retries = 0
        self.gateway_ip = gateway_ip
        self._running = False
        super(Wifi_Deamon, self).__init__()
        #disable wlan powermanagment
        self.interface = self.get_interface()
        self.shell_command(f"sudo iwconfig {self.interface} power off")
        
    def run(self):
        self._running = True
        while(self._running):
            
            if(self.is_gateway_reachable() == False):
                self._retries += 1
                self.reset_WLAN()
                print("resetting WLAN")
            else:
                print("Connection OK")
                self._retries = 0
            
            #reboot
            if(self._retries > 10):
                self.radio_on()
                time.sleep(10)
                self.ip_link_up()
                time.sleep(10)
                self.reboot()
                
            time.sleep(10)
            
    def is_gateway_reachable(self):
        try:
            reachable = False
            
            res = self.shell_command(f"ping {self.gateway_ip} -c 1 | grep 'received' | awk -F',' " +"'{ print $2}' | awk '{ print $1}'")
            print(res)

            if(int(res) == 1):
                reachable = True
                
        except Exception:
            pass
        return reachable
    
    def shell_command(self,input):
        return os.popen(input).read()

    def get_interface(self):
        interface = "wlan1"
        res = self.shell_command("iwgetid")
        if("ESSID" in res):
            interface = res.split("     ")[0]
        return interface

    def get_SSID(self):
        interface = None
        res = self.shell_command("iwgetid")
        if("ESSID" in res):
            interface = res.split('"')[1]
        return interface

    def ip_link_up(self):
        print(self.shell_command(f"sudo ip link set {self.interface} up"))
        
    def radio_on(self):
        print(self.shell_command("sudo nmcli radio wifi on"))
        
    def ip_link_down(self):
        print(self.shell_command(f"sudo ip link set {self.interface} down"))
        
    def is_ip_link_up(self):
        res = self.shell_command(f"cat /sys/class/net/{self.interface}/carrier")
        print(res)
        if(res == "1\n"):
            return True
        else:
            return False

    def radio_off(self):
        print(self.shell_command("sudo nmcli radio wifi off"))
        
    def reboot(self):
        print("rebooting")
        print(self.shell_command("sudo reboot"))
        
    def reset_WLAN(self):
        self.ip_link_down()
        time.sleep(10)
        self.radio_off()
        time.sleep(10)
        while(self.is_ip_link_up() == False):
            self.radio_on()
            time.sleep(10)
            self.ip_link_up()
            time.sleep(15)
        time.sleep(60)
 
if __name__ == '__main__1':
     wlan_ref = Wifi_Deamon("192.168.2.1")
     print(wlan_ref.is_ip_link_up())
            
    
if __name__ == '__main__':
    wlan_ref = Wifi_Deamon("192.168.2.1")
    wlan_thread = Thread(target = wlan_ref.run)
    wlan_thread.start()
    wlan_thread.join()

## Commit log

2024-12-30 get devicename of serialadapter
2025-01-09 Mainboard power reset ugly but working
    [Philips_2200.py]
2025-01-16 Initial commit
    can be used to reset WIFI Connection which can be unstable on HAss RPi
    [Reset_Wifi.py]
2025-01-17 Fix Home Assistant WIFI stability issues
    [Reset_Wifi.py]
2025-01-20 Set Waste, Cup Size, coffee strength & error LEDs
    [Philips_2200.py, Reset_Wifi.py]
2025-01-20 power on with cleaning cycle
2025-01-23 reset wifi: full device activation
    [Reset_Wifi.py]
2025-03-17 Untested PCB + Schematic
    [philips_2200_mitm.kicad_pcb, philips_2200_mitm.kicad_sch]
2025-03-17 untested pcb + sch
